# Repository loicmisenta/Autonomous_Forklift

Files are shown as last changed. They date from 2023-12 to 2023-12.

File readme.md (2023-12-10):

---
title: Autonomous forklift
author: Loïc Misenta, Hadrien Saigot Forest, Inés Araujo Cañas, Athena Papageorgiou Koufidou, Kalil Sama Bouzigues, Dylan Vairoli
---

# Introduction
This project was developed for the CS-356 Making Intelligent Things course at EPFL. The team members are Loïc Misenta, Hadrien Saigot Forest, Inés Araujo Cañas, Athena Papageorgiou Koufidou, Kalil Sama Bouzigues and Dylan Vairoli.

# Overview
The autonomous forklift is a project aimed at automating the movement of packets within a facility. When placing a packet in front of the forklift, it uses a camera to read and process a QR code on the packet. The QR code contains information about the packet's intended location in the facility. The forklift then picks it up and moves in a to the designated location and places the packet on the ground. Upon completion, the forklift returns to its starting position, ready to repeat the process with another packet. Manual controls are also available with a gamepad or a web application.

<!-- add video -->
<video src="report/images/AutonomousForkLiftMIT.mp4" controls="controls" style="max-height: 550px;">
</video>

# Materials

### Microcontrollers
- [ESP32-CAM-MB, USB-to-serial interface for ESP32-CAM](https://www.berrybase.de/en/esp32-cam-mb-usb-zu-seriell-schnittstelle-fuer-esp32-cam)
- [ESP32-CAM Development Board incl. OV2640 camera module](https://www.dfrobot.com/product-1879.html)
- [ESP8266](https://en.wikipedia.org/wiki/ESP8266)
- [Arduino Uno](https://en.wikipedia.org/wiki/Arduino_Uno)

### Motors
- [5 NEMA17-04 stepper motors](https://www.3dware.ch/NEMA-17-Stepper-motor-1.8-degree,-1.2A-En.htm)
- [5 stepper drivers](https://www.fruugoschweiz.com/5pcs-a4988-stepstick-stepper-motor-driver-module-with-heat-sink-for-3d-printer-reprap-suitable/p-117051283-245844502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)
- [Arduino Uno CNC shield](https://www.bastelgarage.ch/cnc-shield-a4988-arduino-fur-3d-drucker-und-frasmaschinen-grbl)

### Electronics
- PCB board
- [2 end switches]("https://www.spplotter.com.br/micro-switch-fim-de-curso-omron-ss-5gl)
- jumper cables

### Power supply
- Conrad Energy Lipo battery 11.1V 5000mAh
- 5V to 10V battery

### Construction
- [Machifit 15pcs 400mm Optical Axis Guide Bearing Housings Linear Rail Shaft Support Screws Set](https://www.fruugoschweiz.com/15pcsset-400mm-optical-guide-bearing-axis-screws-linear-guide-rail-shaft-support-set/p-163505313-347691854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)
- 3d printer filament
- MDF
- screws

# Tools
For this project, we used a Prusa 3D printer and a laser cutter, both available at [The SPOT](https://www.epfl.ch/education/educational-initiatives/discovery-learning-program-2/prototyping/page-111858-en-html/) at EPFL. The 3D printer was used to print the wheels and structures for cable and electronic components management, while the laser cutter was used to create the base platform, boxes and forks. Other tools needed for this project include a soldering iron, a multimeter, a screwdriver and other basic tools.
The software you are going to need is the Arduino IDE and a text editor of your choice.
<!-- List of required tools would go here, e.g. laser cutter, 3d printer etc., perhaps also a note about were to obtain them or where to find access to them -->

# Safety
It is important to be aware of potential risks associated with the tools and processes involved. The use of tools such as 3D printers, laser cutters, soldering irons, and other equipment can pose certain hazards. When operating these tools, there is a risk of burns, electric shocks, or injuries from moving parts. To mitigate these risks, it is crucial to follow safety guidelines provided by the tool manufacturers and wear appropriate personal protective equipment (PPE) such as safety glasses, gloves, and closed-toe shoes. Ensure that the work area is well-ventilated and free from clutter, providing a safe environment for operating tools. Take precautions when handling hot or sharp objects, and avoid touching heated surfaces directly. Additionally, exercise caution when working with electrical components or circuits, ensuring proper insulation, grounding, and adherence to safe soldering practices. Regularly inspect and maintain the tools and equipment to ensure they are in good working condition. 

# Construction

<figure>
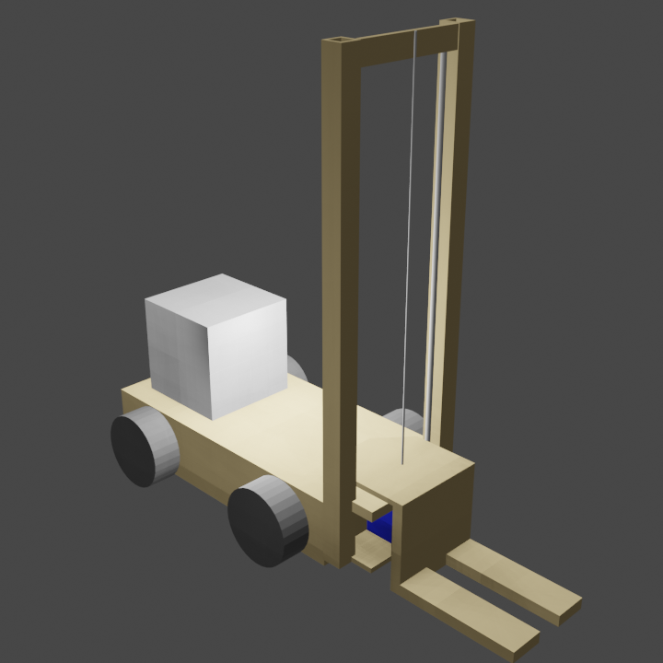
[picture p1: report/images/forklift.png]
  
  <figcaption>Initial idea of the forlift, made with Blender</figcaption>
</figure>

<figure>
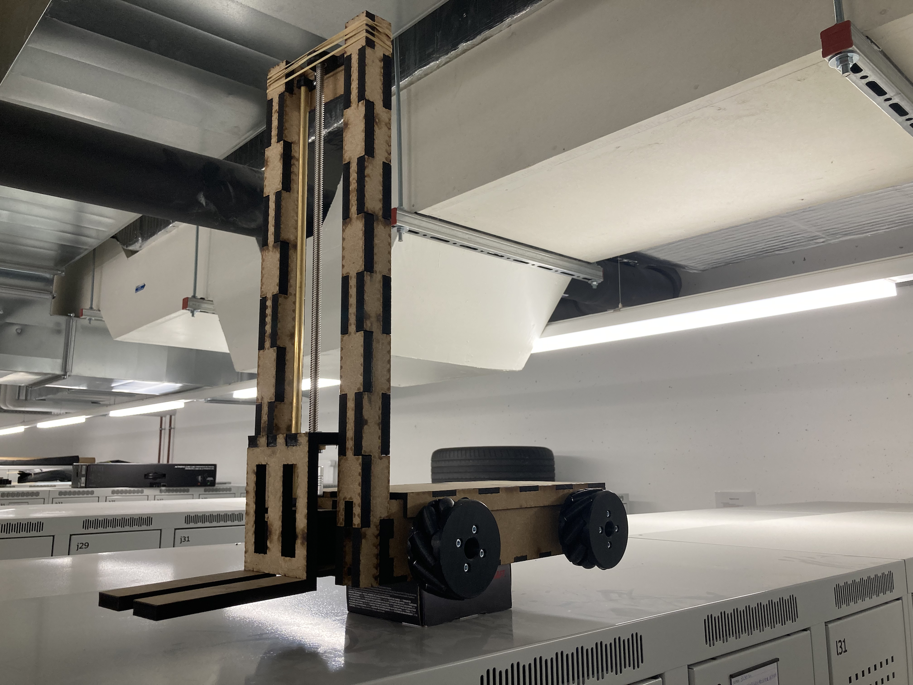
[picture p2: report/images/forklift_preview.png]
  
  <figcaption>Final forklift design.</figcaption>
</figure>

We decided to go with MDF as the primary material for our forklift. It is quite cheap and easily modifiable, while we were prototyping we could quickly drill some new holes and so on.

## Base

<figure>
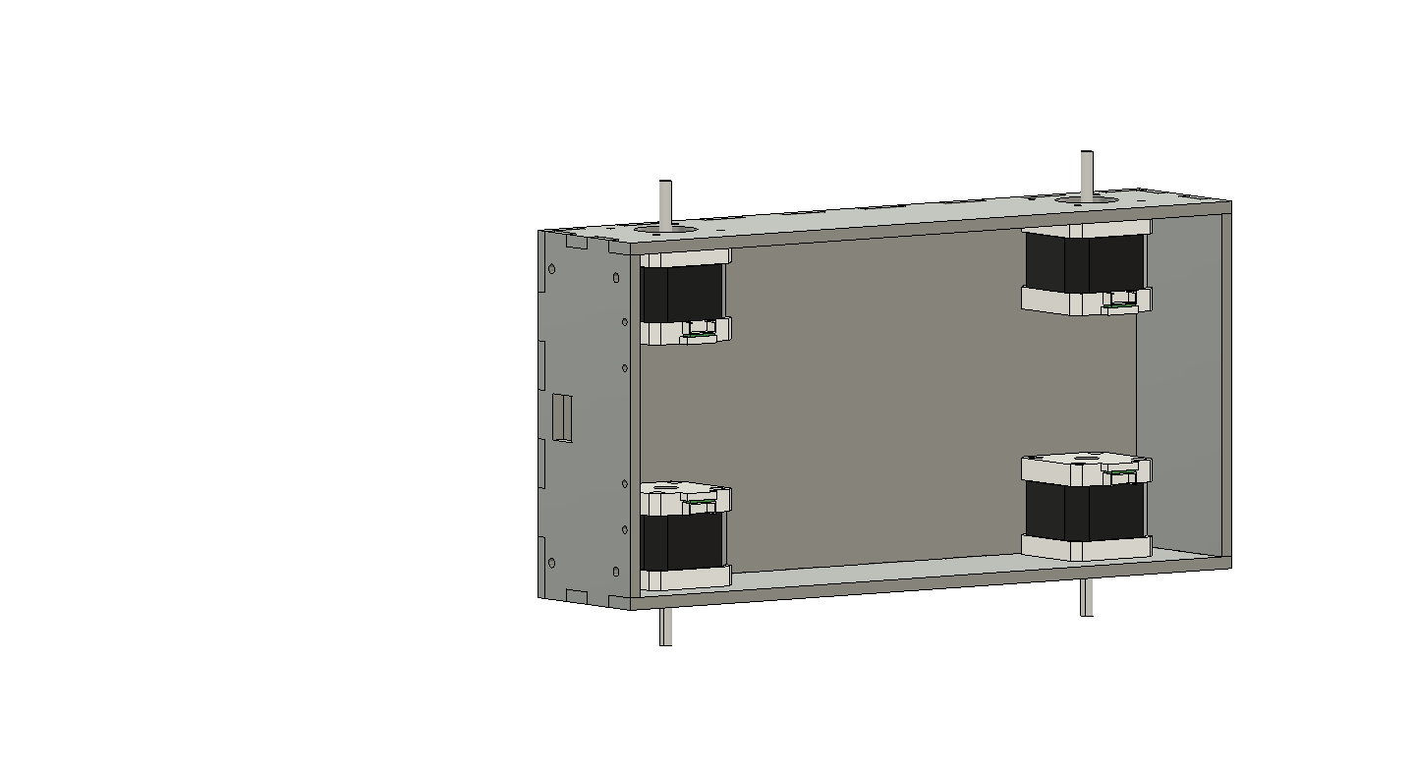
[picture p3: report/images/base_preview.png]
  
  <figcaption>Base of the forklift body.</figcaption>
</figure>

We took the base from the [Arduino Mecanum Wheels Robot](https://howtomechatronics.com/projects/arduino-mecanum-wheels-robot/) project by [Dejan](https://howtomechatronics.com/author/howtom12_wp/) that we slightly adapted to use comb joints and have some more holes so that we can glue parts together and pass cables through it.

You can find the `.dxf` file for this at [`Modeling/Body/base.dxf`](https://gitlab.epfl.ch/papageor/cs-356-autonomous-forklift/-/blob/main/Modeling/Body/base.dxf)

## Side supports

<figure>
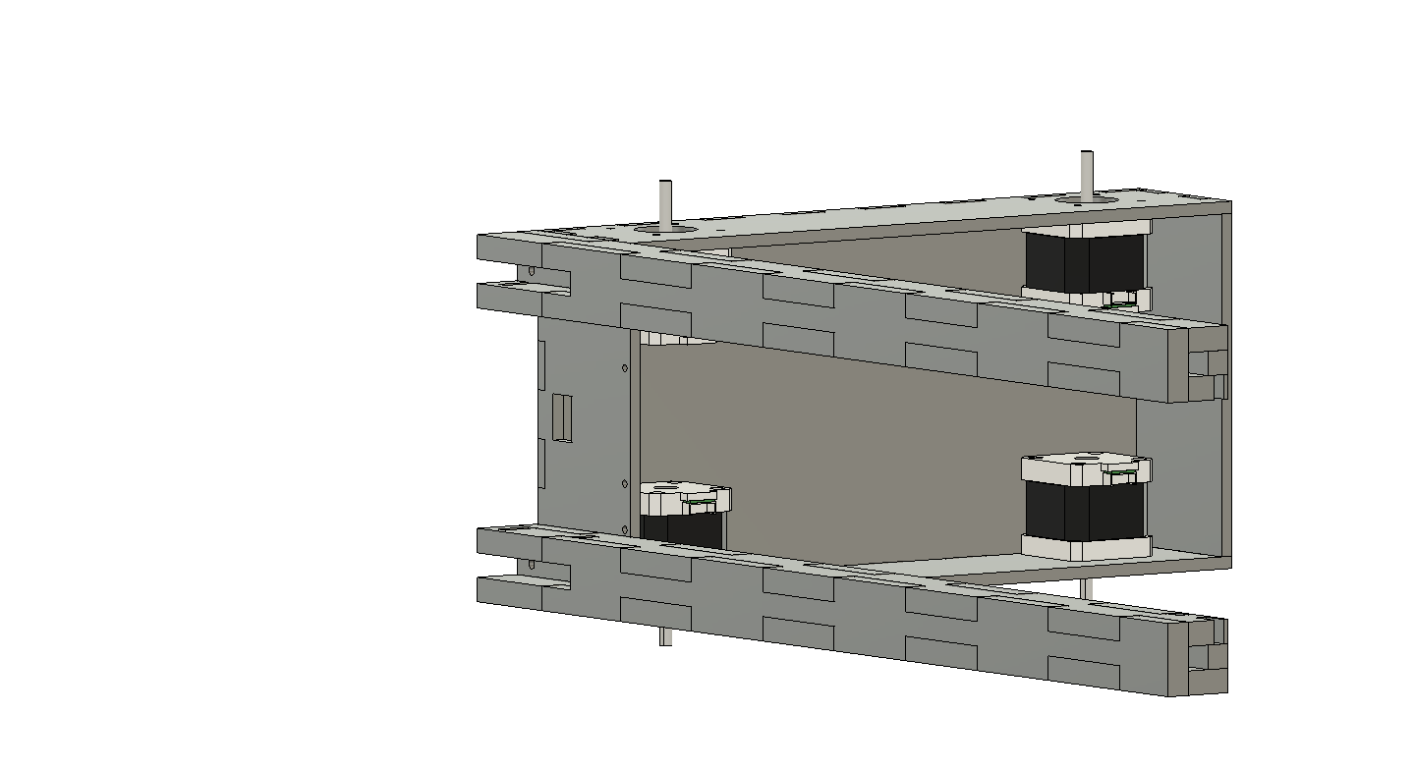
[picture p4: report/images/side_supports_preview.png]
  
  <figcaption>Side supports of the forklift.</figcaption>
</figure>

We designed some side supports to attach the two side shafts on which the forks are drilled. They are quite massive but it was giving a nice raw look to the forklift.

You can find the `.dxf` file for this at [`Modeling/Body/side_supports.dxf`](https://gitlab.epfl.ch/papageor/cs-356-autonomous-forklift/-/blob/main/Modeling/Body/side_supports.dxf)

## Cap

<figure>
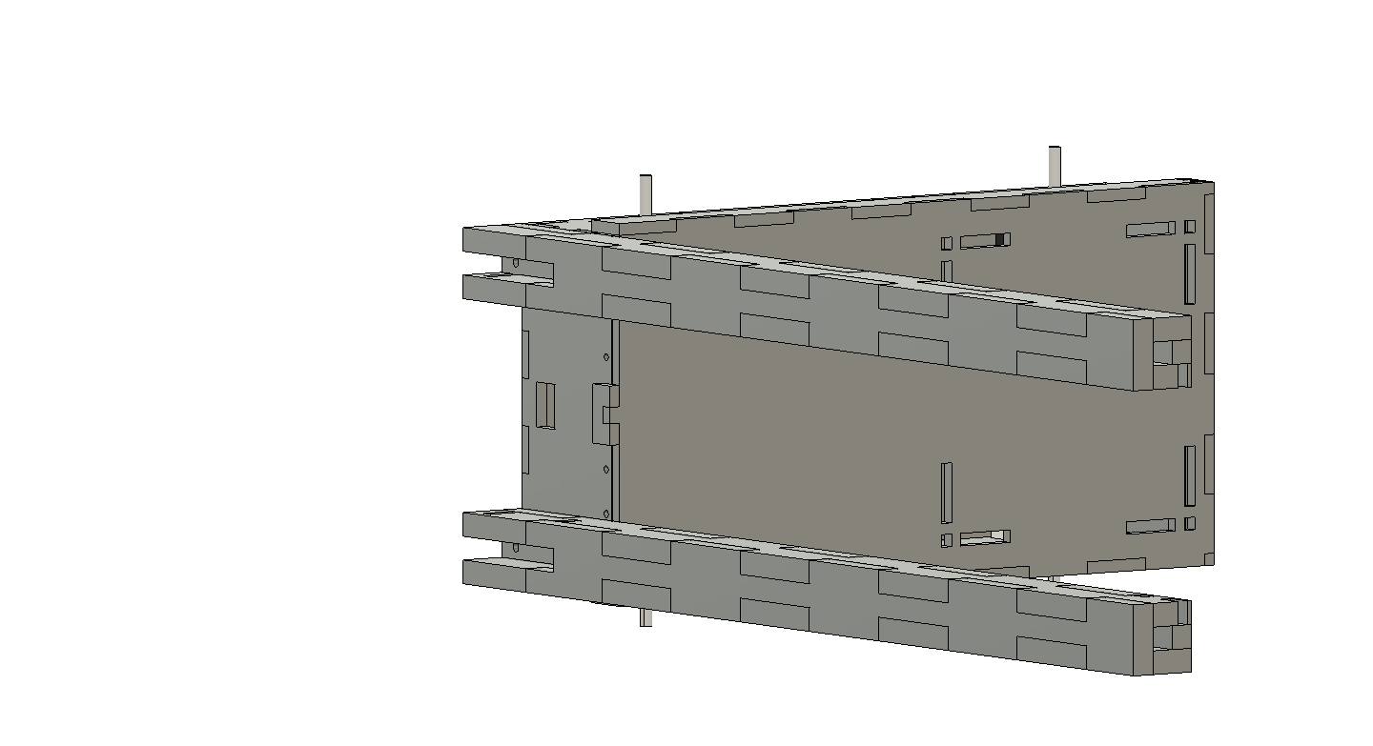
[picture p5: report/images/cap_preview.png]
  
  <figcaption>Cap of the forklift.</figcaption>
</figure>

Also using this comb joints technique, we added a cap that can easily be removed on top of the base platform. It gives a polished and refined aspect to our vehicle by hiding all the cables.

You can find the `.dxf` file for this at [`Modeling/Body/cap.dxf`](https://gitlab.epfl.ch/papageor/cs-356-autonomous-forklift/-/blob/main/Modeling/Body/cap.dxf).

## Forks

<figure>
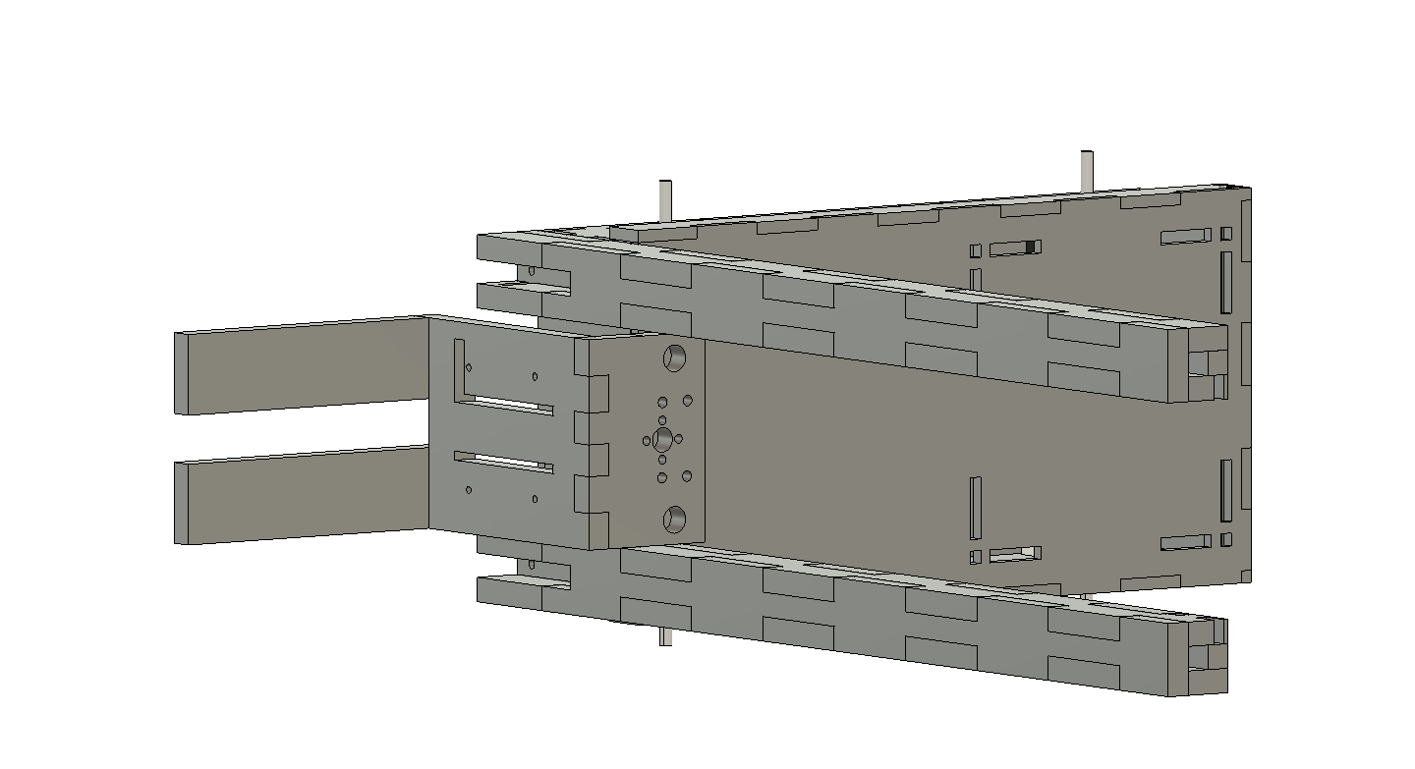
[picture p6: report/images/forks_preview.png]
  
  <figcaption>Forks of the forklift.</figcaption>
</figure>

Obviously, we also had to create the forks that are used to take the boxes. Our first try was a failure because it was too thin and couldn't lift anything without breaking. This final model works better but it still needs brackets to support at least two kilograms. We 3D-printed them because we couldn't get any metal one, but 10x10mm metal brackets are enough.

You can find the `.dxf` file for this at [`Modeling/Body/forks.dxf`](https://gitlab.epfl.ch/papageor/cs-356-autonomous-forklift/-/blob/main/Modeling/Body/forks.dxf). You can also find the `.stl`file for the brackets at [`Modeling/Body/bracket.stl`](https://gitlab.epfl.ch/papageor/cs-356-autonomous-forklift/-/blob/main/Modeling/Body/Bracket.stl).

## Fixation panels

<figure>
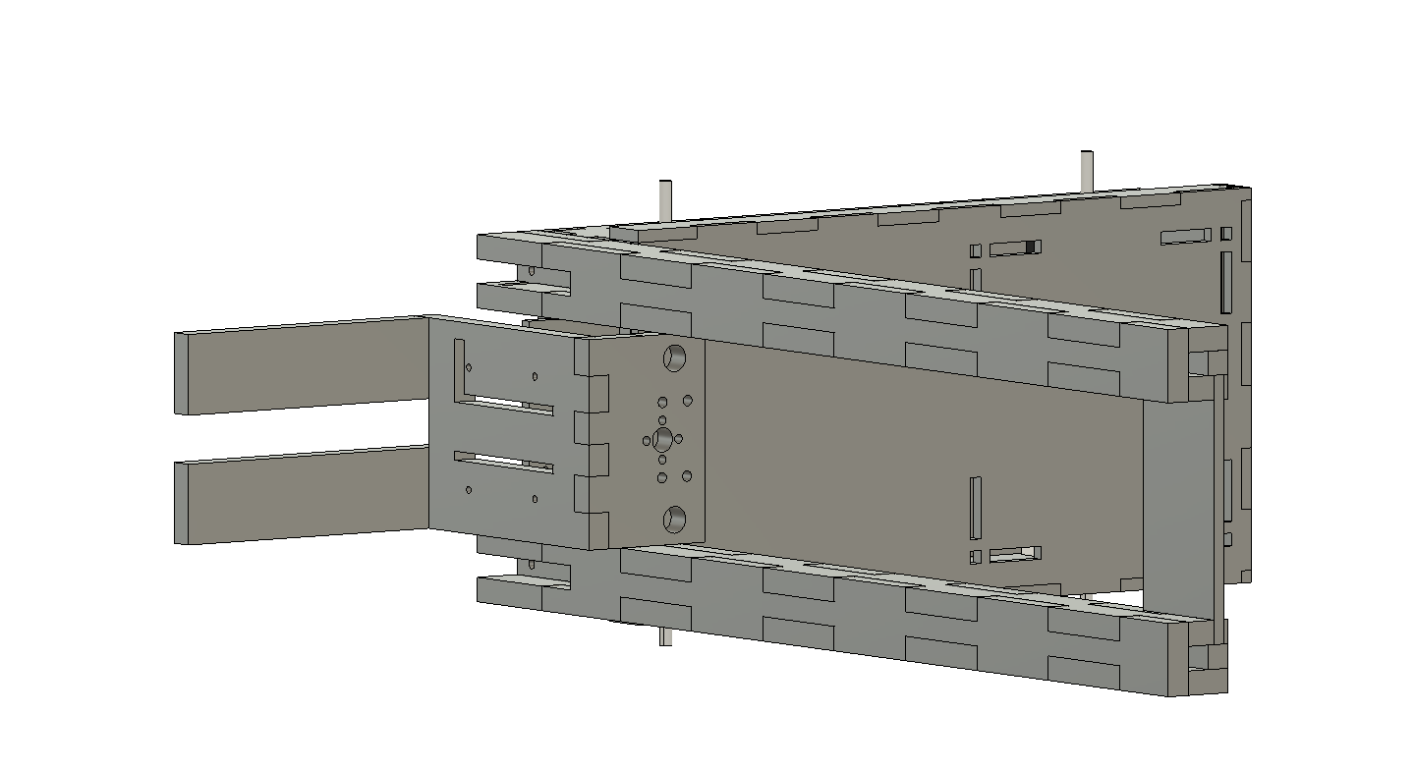
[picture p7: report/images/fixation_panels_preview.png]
  
  <figcaption>Fixation panels of the forklift.</figcaption>
</figure>

Finally, we added some MDF fixation panels to attach our components such as the vertical stepper motor and the three shafts.

You can find the `.dxf` file for this at [`Modeling/Body/fixation_panels.dxf`](https://gitlab.epfl.ch/papageor/cs-356-autonomous-forklift/-/blob/main/Modeling/Body/fixation_panels.dxf).

## Fixations

<figure>
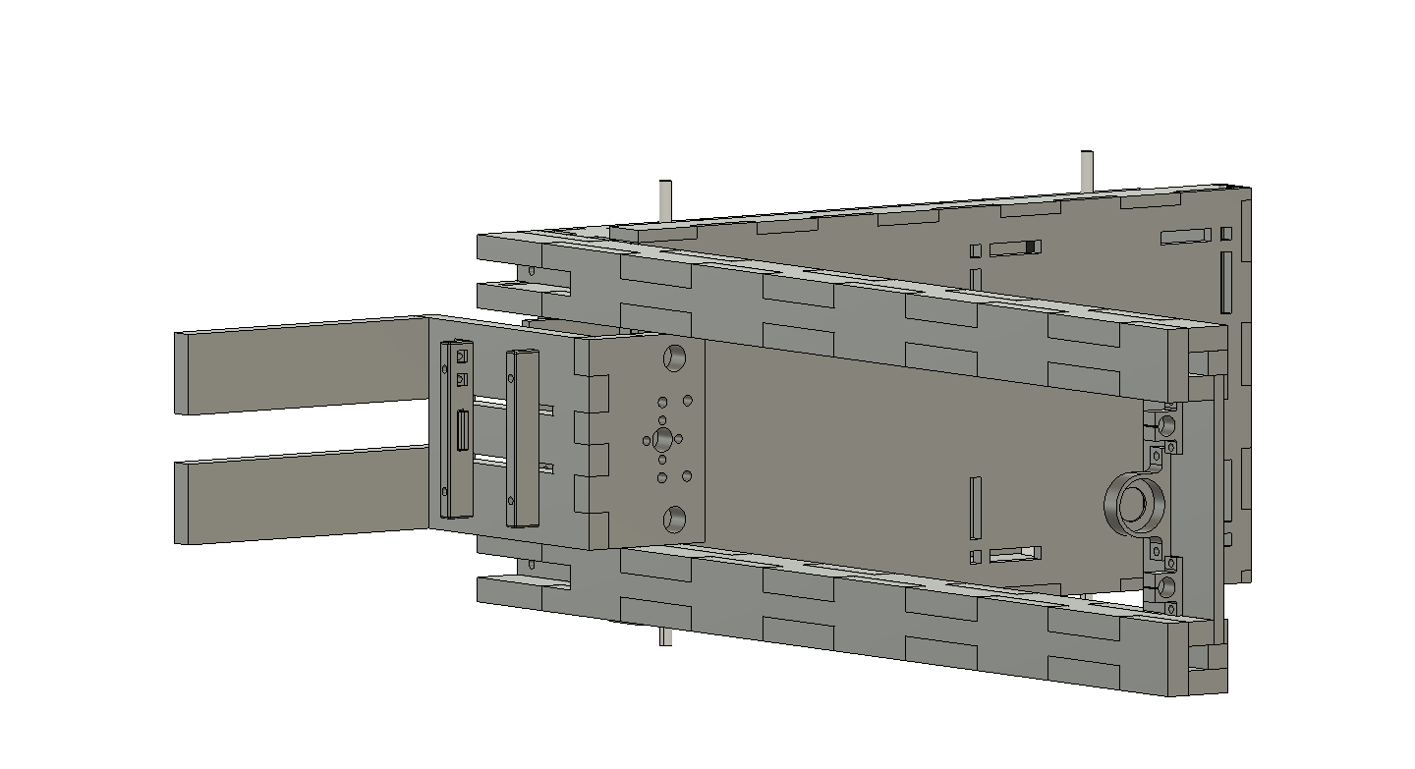
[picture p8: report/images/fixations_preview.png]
  
  <figcaption>Fixations of the forklift.</figcaption>
</figure>

Along the way, we encountered small issues for which we had to design some small 3D-printed pieces
- To hold the two side shafts
- To hold the central screw shaft
- To attach the forks to the block bearings
- To keep the vertical end switch at the right position
- To avoid that the side shafts get out of the fixations when lifting up. Because our block bearings didn't slide perfectly smoothly along our shafts, we needed some caps to force them to stay inside the fixations
- To hold the ESP32-CAM against the forks as well as the horizontal end switch
  
You can find the `.stl` files for these pieces at [`Modeling/Fixations/`](https://gitlab.epfl.ch/papageor/cs-356-autonomous-forklift/-/tree/main/Modeling/Fixations).

## Cable management
To keep our circuit clean and avoid short circuits because of floating components, we designed structures to cleanly manage our cables. 

- One that is used to wrap the cables around
- One to screw our PCB board to the base
- One to attach the ESP8266 to the base

However all of these pieces are very specific to our usecase so it may not suit perfectly your components.
  
You can find the `.stl` files for these pieces at [`Modeling/Cable Management/`](https://gitlab.epfl.ch/papageor/cs-356-autonomous-forklift/-/tree/main/Modeling/Cable%20Management).

## Counterweight box

<figure>
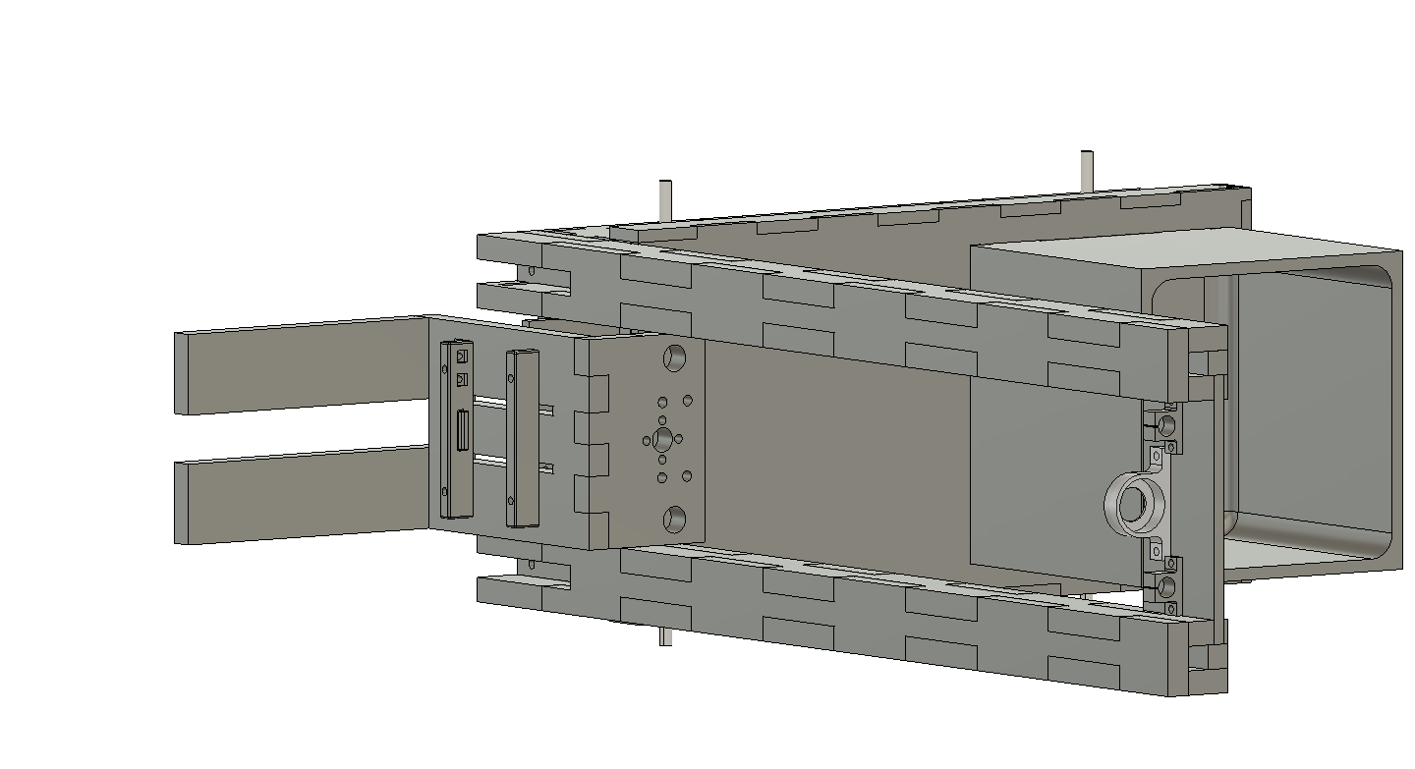
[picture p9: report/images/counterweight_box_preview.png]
  
  <figcaption>Counterweight box of the forklift.</figcaption>
</figure>

Any forklift needs some counterweight at the back of it to balance with the weight it is carrying. To do so, we opted for a 3D-printed box with round edges so that nothing gets stuck in them. You can then fill it with whatever you want, rocks or sand for example.

You can find the `.stl` files for this at [`Modeling/Body/counterweight_box.stl`](https://gitlab.epfl.ch/papageor/cs-356-autonomous-forklift/-/blob/main/Modeling/Body/counterweight_box.stl).

## Mecanum wheels

<figure>
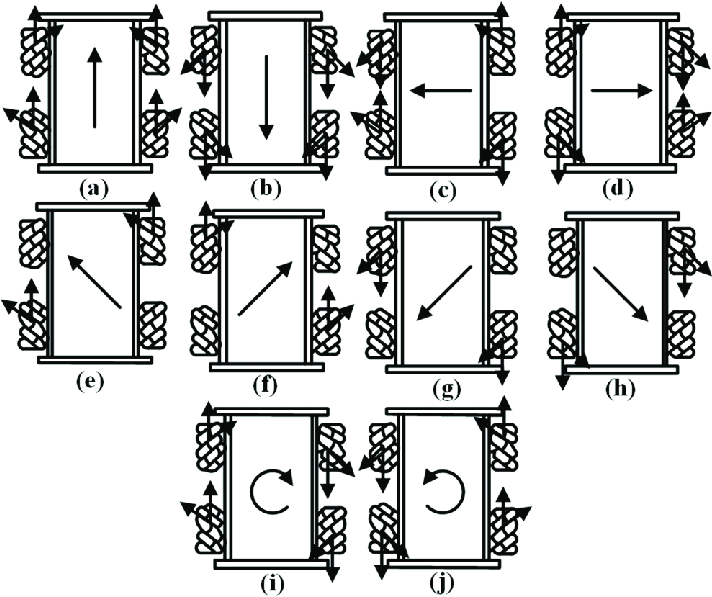
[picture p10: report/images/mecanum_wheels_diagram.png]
  
  <figcaption>Mecanum wheels  combinations diagram (<a href="https://www.researchgate.net/figure/Fig-5-Top-view-of-turning-principle-of-Mecanum-wheel_fig2_307868549">source</a>).</figcaption>
</figure>

Mecanum wheels allow you to move sideways, turn in place as well as go diagonally with only 4 independent wheels. By turning the wheels with a specific combination of directions, you can achieve the desired effect.

We used the [Arduino Mecanum Wheels Robot](https://howtomechatronics.com/projects/arduino-mecanum-wheels-robot/) project as a basis for our wheels. You can either download the `.stl` files from his tutorial or you can find them under [Modeling/Wheels](https://gitlab.epfl.ch/papageor/cs-356-autonomous-forklift/-/tree/main/Modeling/Wheels). Pay attention to print two right wheels and two left wheels. For more details about the mounting of these wheels, you can check [Dejan's tutorial](https://howtomechatronics.com/projects/arduino-mecanum-wheels-robot/).

> Note that we had to slightly modify the outer part of the wheels because we did not have any M3 bolts that were 45mm long, only 40mm.

# Motors and electronics

## A4988 stepper driver
We used A4988 stepper drivers to control our steppers. However we need to limit the output current they produce to 1.5A. To do so we need to adjust the small screw on top of them. Follow the _A4988 Current Limiting_ section of [Stepper Motors and Arduino – The Ultimate Guide by Dejan](https://howtomechatronics.com/tutorials/arduino/stepper-motors-and-arduino-the-ultimate-guide/).

## CNC Shield and Arduino UNO

<figure>
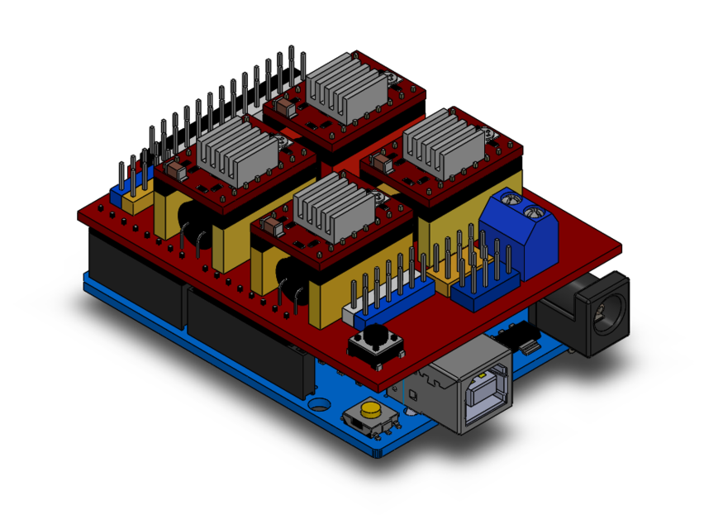
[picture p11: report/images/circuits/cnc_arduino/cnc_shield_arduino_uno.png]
  
  <figcaption>CNC shield and drivers on top of an arduino UNO (<a href="https://grabcad.com/library/arduino-uno-cnc-shield-1">source</a>).</figcaption>
</figure>

<figure>
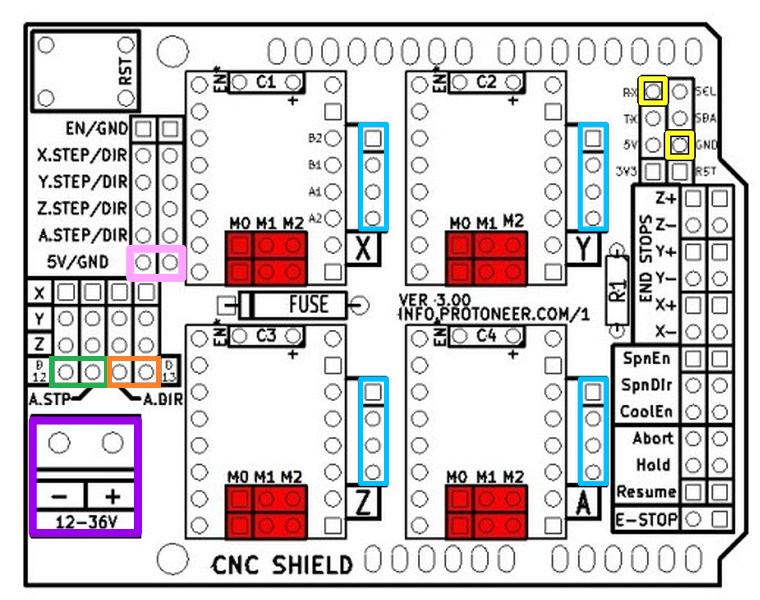
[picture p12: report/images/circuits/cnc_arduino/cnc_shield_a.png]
  
  <figcaption>CNC shield closeup (<a href="https://forum.arduino.cc/t/arduino-uno-cnc-shield-controlling-4-stepper-motors/913742/3">source</a>).</figcaption>
</figure>

The CNC shield is very simple to use, you just need to plug it on top of the Arduino UNO and install the drivers on top of it.

However be careful with a few points:

- The `Enable` pin of the drivers should be at the position marked as `EN` on the shield.
- As we use the 4 steppers independently, we need to indicate that the `A` (red) driver is controlled on its own. This is done by connecting a jumper at the green and orange spots in the image above. ([source](https://www.zyltech.com/arduino-cnc-shield-instructions/)).
- For smoother movement, we decided to use 16x microstepping. This is not mandatory but it works best with the mecanum wheels in our opinion. To do so, you need to connect jumper wires on all the `M0`, `M1` and `M2` pins. You can find more information about other microstepping resolutions [here](https://www.zyltech.com/arduino-cnc-shield-instructions/).
- When plugging in the motors, they might turn in the incorrect direction or you might have plugged steppers in different locations as us. You can test this by uploading the `steppers_test.ino` sketch to the Arduino UNO. It should start turning the steppers clockwise in this order: back left, front left, back right, front right. If they turn counter-clockwise instead, you need to turn their cables by 180 degrees. If they turn in an incorrect order, try to switch the positions where they're plugged in the shield accordingly. 
- You can find the mapping between the Arduino UNO pins number and the actual controls of the shield in the `arduino_main.ino` sketch.

## ESP8266
Unfortunately the Arduino UNO we used does not have WIFI capabilities. As we needed to transfer instructions from the computer using WIFI to our boards, we used an ESP8266. We can consider it as the brain of our circuit, it receives the instructions from the computer online and dispatch it either to the Arduino UNO to move the wheels or to itself to control the vertical stepper. As we just mentioned, it is also responsible to control the vertical stepper motor because the Arduino UNO had all of its pins busy with the shield.

## ESP32-CAM
To scan QR codes we needed a camera, the ESP32-cam was perfect for that as it also has WIFI capabilities. When reading a QR code, it sends its payload (which is simply a number) to the computer which then send the correct instruction to the ESP8266 based on the number it received.

## NEMA 17 stepper motors
We use 5 NEMA17 stepper motors; 4 for the wheels and one for the forks. They are strong motors capable of lifting up our boxes. You can find more information about how stepper motors work [here](https://howtomechatronics.com/how-it-works/electrical-engineering/stepper-motor/)

## Conrad Energy Lipo battery 11.1V 5000mAh
As a power supply for our steppers and the Arduino UNO, we used a 12V Lipo battery.

## 5V to 10V battery
You will also need any kind of 5V to 10V power source for the ESP8266 because it can't take the 12V of the Lipo battery.

## End switches

<figure>
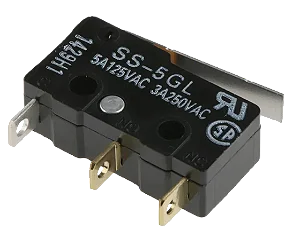
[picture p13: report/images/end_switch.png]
  
  <figcaption>Microswitch Omron SS 5GL (<a href="https://www.spplotter.com.br/micro-switch-fim-de-curso-omron-ss-5gl">source</a>).</figcaption>
</figure>

We used two end switches in our project. The first one is used to know when the forks are at the bottom and we should stop, the other one is used to know when a box is entirely placed on the forks.

# Circuits

## CNC shield
- Connect the stepper cables to the blue area in the above schema.
- Add jumpers between the two green pins and between the two orange pins to control the A slot as well.
- Add jumpers between the `M0`, `M1` and `M2` (red) pins to enable 16x microstepping.
- Connect a 12V power source to the purple area above and to the Arduino UNO.

## ESP8266
- Connect a 5V to 10V power source to the `VIN` and `GND` pins of the ESP8266.

## ESP32
- Connect the `5V` and the `GND` pins of the ESP32 to the `5V` and `GND` pins (pink) of the CNC shield. 

## ESP8266 – Arduino UNO serial communication
- Connect the `D4` and the `GND` pins of the ESP8266 to the `RX` and `GND` pins (yellow) of the CNC shield.

## End switches
- Connect one of the extremity pins of the two end switches to the `3V` pin of the ESP8266.
- Connect the middle pin of the vertical end switch to the `D5` pin of the ESP8266.
- Connect the middle pin of the horizontal end switch to the `D1` pin of the ESP8266.
- Connect the `GND` pin of the ESP8266 to the middle pins of the end switches through a 10k$\Omega$ resistor.

# Software

<figure>
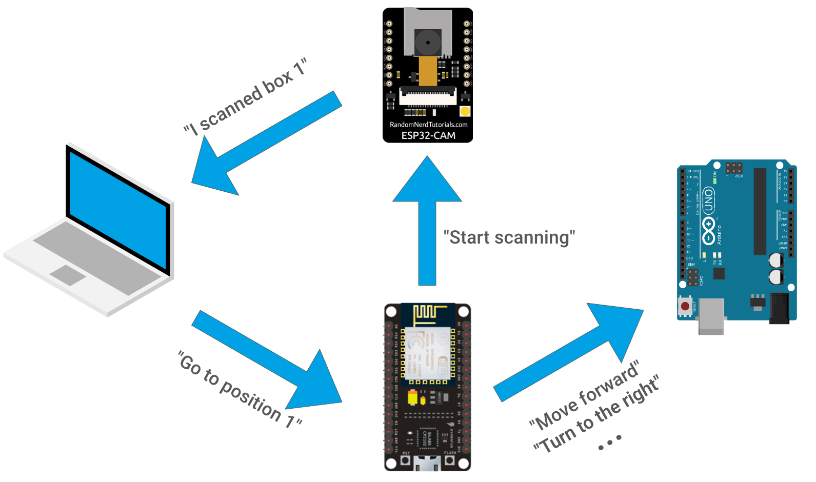
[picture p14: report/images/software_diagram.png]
  
  <figcaption>Software diagram.</figcaption>
</figure>

## Arduino UNO
The Arduino UNO is only responsible to move the wheels of the forklift. It receives instructions from the ESP8266 about where to go using serial communication. We used the `AccelStepper` library to control our steppers.

You can find Arduino-related code at [Code/arduino-main](https://gitlab.epfl.ch/papageor/cs-356-autonomous-forklift/-/tree/main/Code/arduino-main).

## ESP8266
The ESP8266 is the brain of our forklift. It receives instruction from the computer using WIFI and dispatch them correctly to the Arduino UNO if needed, to itself otherwise. It keeps track of the positions of our grid and the current state of the forklift. It also controls the vertical stepper motor.

You can find ESP8266-related code at [Code/esp8266-main](https://gitlab.epfl.ch/papageor/cs-356-autonomous-forklift/-/tree/main/Code/esp8266-main).

## Web clients
To send instructions to the ESP8266's server, we need a web client running on the computer. 

### Web application client
The first one can send intructions by clicking on buttons in a custom UI. You can tell the forklift to go in a particular direction or to pickup a box and to put it at a specific position. It can be found at [Code/webapp](https://gitlab.epfl.ch/papageor/cs-356-autonomous-forklift/-/tree/main/Code/web-clients/webapp).

<figure>
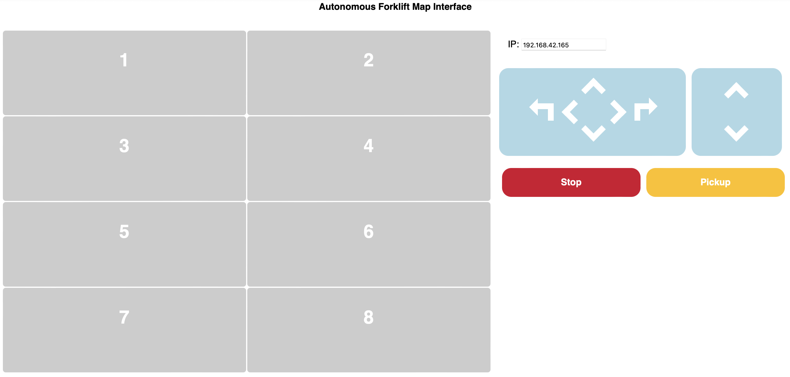
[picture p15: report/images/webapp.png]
  
  <figcaption>Web interface to control the forklift.</figcaption>
</figure>

### Gamepad client
The second one controls the forklift with a gamepad connected to the computer. Simply open [Code/web-clients/gamepad_client.html](https://gitlab.epfl.ch/papageor/cs-356-autonomous-forklift/-/blob/main/Code/web-clients/gamepad_client.html), if a gamepad is detected it will be displayed. Enter the correct IP for your ESP8266 and make sure that it is connected to the same WIFI as your computer. You can change WIFI credentials in [Code/esp8266-main/esp8266-main.ino](https://gitlab.epfl.ch/papageor/cs-356-autonomous-forklift/-/blob/main/Code/esp8266-main/esp8266-main.ino). 

<figure>
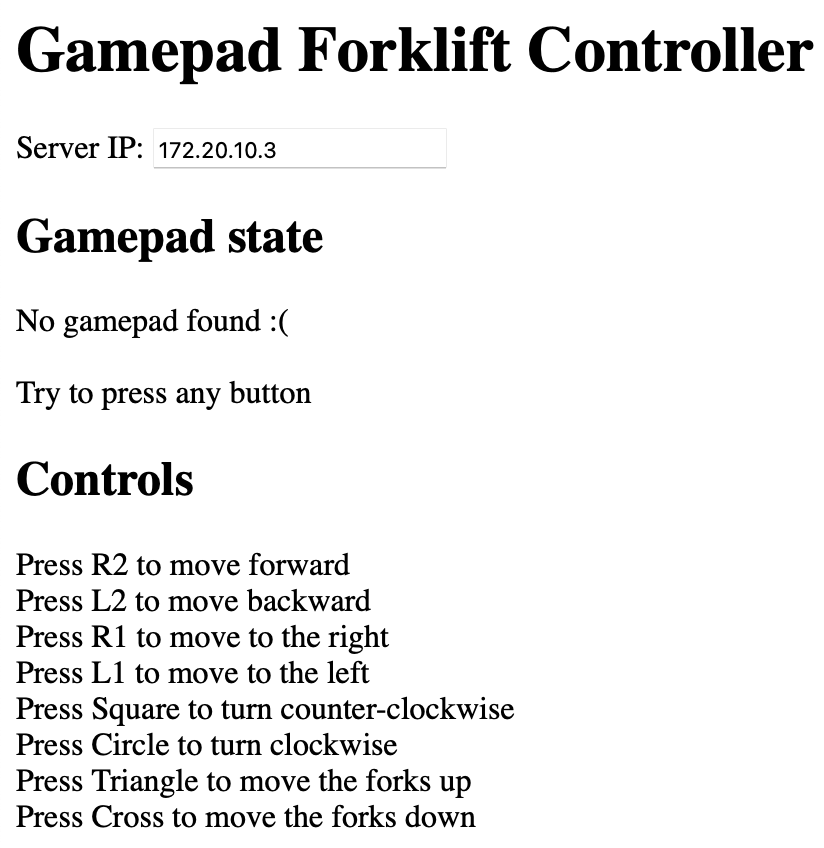
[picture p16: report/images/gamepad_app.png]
  
  <figcaption>Gamepad web controller</figcaption>
</figure>

### QR code recognition
We can also send instructions to the ESP8266 by scanning a QR code. The QR code should contain a number between 1 and 6. The ESP8266 will then move the forklift to the corresponding position in the facility. You can find the code for this at [QR_Code](https://gitlab.epfl.ch/papageor/cs-356-autonomous-forklift/-/tree/main/QR_Code).

The QR code handling is a big part of the project. The way it works is the following. The ESP32-
CAM scan the QR Code present on the box, send the id number of the box to the computer 
which has a .csv file with all the data that corresponds to the box, then send the placement of 
the box to the ESP8266 that can after move appropriately given the information that was in the 
.csv file. The ESP8266 is also responsible for telling the ESP32-CAM to start scanning QR code.

<figure>
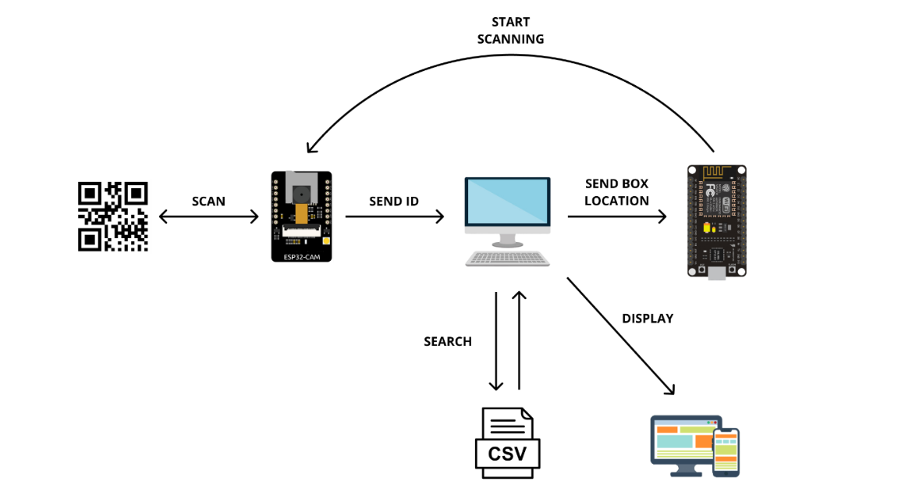
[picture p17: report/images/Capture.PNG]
  
  <figcaption>QR code recognition</figcaption>
</figure>

### Implementation
There is 3 files : [QR_CODE_CSV_2.ino](https://gitlab.epfl.ch/papageor/cs-356-autonomous-forklift/-/blob/main/QR_Code/QR_CODE_CSV_2/QR_CODE_CSV_2.ino), [data.csv](https://gitlab.epfl.ch/papageor/cs-356-autonomous-forklift/-/blob/main/QR_Code/QR_CODE_CSV_2/data.csv), [server.js](https://gitlab.epfl.ch/papageor/cs-356-autonomous-forklift/-/blob/main/QR_Code/QR_CODE_CSV_2/server.js).

#### QR_CODE_CSV_2.ino
In the Arduino file there is multiple sections.  
The first section is the configuration of the server of the ESP32, the connection to the server 
of the computer, the initialisation of camera and the handling of HTTP request coming from the 
ESP8266. 
The second one is the handling of the QR code scan. In this section the scanning will begin 
only if the ESP8266 want a scan. If so it will search for a QR code and if it finds one, it send the 
id found by an HTTP request to the server running on the computer. If there is no error a flash 
will be done to have a visual confirmation that the id was correctly sent. 
The third part is where the server, the client, the camera are all setup correctly to handle all 
situation

#### data.csv
This file contains a table of 3 columns : id, type and description. The id is used to know what 
box it is and where it is going, the type and the description are for the display on the webpage 
to know what is inside. 

#### server.js
This is where the local server on the computer is setup. When it received an http request with 
the id, it will scan each row of the csv file to get all the information needed to send to ESP8266.

### Problems encountered
The main problem that I have encountered is the scanning of the QR Code. I spent a lot of time 
finding and understanding the libraries for scanning. There were many of them so I have to tried 
many to find the best. In this project we wanted to scan quick, also the main question was : 
“What do I put in my QR Code ?”. At first I tried to put a JSON text but the camera detect it very 
slowly so I tried to find some compression algorithms like “shoco” which compress little string 
but not efficient. Finally I found a way to have only a little information on the QR, an id, and all 
the rest on a csv file on the computer. But to do this I have to learn JavaScript and how to create 
a server, with Node in my case.  
Another problem was the voltage of the ESP32-CAM. This one randomly give an infinite loop of 
error misunderstanding. At first I was thinking it was my code, so I spent few days to recode all. 
After a deep search I found that this ESP32-CAM needs 5V and not 3V when it used a lot of 
resources, like QR Code scanning. But I was using my ESP8266 to send, and decode code so 
it was relies with the 3V of the ESP8266. 
I wrote these line for you to know where I spent my time and to help others students in the 
future to not spending weeks and weeks to debug.

## Navigation
There are several navigation options that can be used to guide the vehicle to the correct path. Since the forklift will be moving in a known facility, we decided to use a form of graph-based navigation, i.e. to divide the facility into a grid of possible positions or nodes, with edges connecting the nodes representing possible paths that the forklift can take. The forklift can use this graph to find the shortest path to a destination node based on its current position and the instructions associated with each node. This approach is simple and easy to implement, as it does not require complex sensors or computer vision algorithms and efficient, as the graph can be precomputed and stored, making the navigation process faster. 

This form of navigation proved to be sufficient for our use case, as the forklift was able to reach its destination with accuracy and without any issues. However, it is not the most robust solution, as it does not account for obstacles or other dynamic changes in the environment. For example, if a box is placed in the middle of the path, the forklift will not be able to detect it and will continue to move forward, potentially colliding with the box. To address this issue, we could use a combination of graph-based navigation and computer vision, where the forklift can use the graph to find the shortest path to the destination and use computer vision to detect obstacles and avoid collisions. This approach would be more robust, as it would allow the forklift to adapt to changes in the environment and avoid obstacles. However, it would also be more complex to implement, as it would require more sensors and computer vision algorithms.

Another possible implementation was using a map where each position are represented as 2D vectors, the x-component is the horizontal distance to travel for the forklift to reach the box in that position and the y-component is the vertical distance to travel from the starting point to where the box stands in that given position. This way we can make any large number of boxes and the map will be made accordingly using a function with a for-loop. The thing is that, in real life the wheels slip a little§ bit on the floor, and even if each box are spaced by a certain equal distance, the vertical distance to each box are not exactly multiple of the vertical step. In that way, we had to recalibrate those steps with some arbtrary coefficient and measure every vertical distance to each position. 

# Conclusion
This project was a great opportunity to learn about the different aspects of robotics, from the mechanical design and construction of the forklift to the electronics and software implementation. We were able to apply the concepts learned in class to a real-world application, which allowed us to gain a better understanding of the material. We also learned how to use new tools and technologies, such as Fusion 360, Arduino, and ESP8266, which will be useful for future projects. Overall, we are satisfied with the results of the project, as we were able to successfully implement the forklift and achieve our goal of automating the movement of packets within a facility.

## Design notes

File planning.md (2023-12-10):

# Current status
- The ESP32 can read QR Code information (that is encoded) and send the information (that is decoded) on the webserver
- The platform is able to move in any direction using the mecanum wheels.
- The fork assembly is attached to the base platform.
- Some boxes to test the fork assembly have been created.

# Planning
## Weeks 10 and 11

At the end of week 11, we should have a working prototype of the forklift that can move around the facility and place boxes to the requested location. The forklift will be able to navigate the facility using a grid system and communicate with a server to receive instructions. The forklift will be able to detect the location of the boxes using a camera and QR codes.

### Navigation: (Athena)
- Implement the algorithm for navigating the grid.
- Write code to improve the accuracy of the navigation algorithm by testing and fine-tuning values.

### Communication: (Dylan and Loic)
- Establish communication between ESP32 and Arduino Uno by writing code for both devices to send and receive data and figuring out the electronics needed (Arduino UNO doesn't have wifi).
- Run a server to test the communication between the devices by sending different types of data.
- Develop a plan for adding the camera, including designing the circuit and writing the code to transmit data from ESP32 to ESP8266 to Arduino.

### Boxes and Facility:(Hadrien)
- Redesign the boxes to be compatible with the new forks by analyzing the dimensions and determining what changes are necessary.
- Create a design for the facility in which the forklift will move by considering the size of the space, obstacles, and the location of the boxes. (we need a floor!!!)

### Forks (Ines and Hadrien and Kalil):
- Ensure that the fork assembly can move vertically to the requested height by designing and implementing a motor control system.
- Add end-switches to the forks to recalibrate the motor at the bottom and detect when the forks are at the bottom of a box by designing and implementing a circuit and code to interface with the switches.

### Camera and QR code (Loic)
- Create a database based on ID  and location of the boxes. The QR code will will contain th eID of the box
- Make the webserver able to send the location of the box to the forklift

### Documentation (all)
- Create documentation for all components of the system, including the code, hardware, and design files.
- Ensure that the documentation is clear, concise, and easy to understand.

### Testing (all)
- Conduct comprehensive testing of the entire system, including navigation, communication, and fork operation.
- Identify and fix any issues discovered during testing.

## Weeks 12 and 14

The schedule for the last weeks will depend on the progress made during the first two weeks. If the forklift is not fully functional by the end of week 11, we will continue working on the tasks from the previous weeks. If the forklift is fully functional, we will work on the following extensions:

- The forklift should be able to stack boxes on top of each other.
- The forklift should be able to pick up boxes from the self and bring them back to the starting point.

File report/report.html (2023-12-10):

# Autonomous forklift

Loïc Misenta, Hadrien Saigot Forest, Inés Araujo Cañas, Athena Papageorgiou Koufidou, Kalil Sama Bouzigues, Dylan Vairoli

# Introduction

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

# Overview

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

# Materials

### Microcontrollers

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

### Motors

- 5 NEMA17-04 stepper motors (https://www.3dware.ch/NEMA-17-Stepper-motor-1.8-degree,-1.2A-En.htm)
- 5 stepper drivers (https://www.fruugoschweiz.com/5pcs-a4988-stepstick-stepper-motor-driver-module-with-heat-sink-for-3d-printer-reprap-suitable/p-117051283-245844502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)
- Arduino Uno CNC shield (https://www.bastelgarage.ch/cnc-shield-a4988-arduino-fur-3d-drucker-und-frasmaschinen-grbl)

### Electronics

- PCB board
- 2 end switches
- jumper cables

### Power supply

- Conrad Energy Lipo battery 11.1V 5000mAh
- 5V to 10V battery

### Construction

- Machifit 15pcs 400mm Optical Axis Guide Bearing Housings Linear Rail Shaft Support Screws Set (https://www.fruugoschweiz.com/15pcsset-400mm-optical-guide-bearing-axis-screws-linear-guide-rail-shaft-support-set/p-163505313-347691854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)
- 3d printer filament
- MDF
- screws

# Tools

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

# Safety

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

# Construction

my alt text

Initial idea of the forklift, made with Blender.

my alt text

Final forklift design.

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

## Base

my alt text

Base of the forklift body.

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

## Side supports

my alt text

Side supports of the forklift.

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

## Cap

my alt text

Cap of the forklift.

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

## Forks

my alt text

Forks of the forklift.

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

You can find the .dxf file for this at Modeling/Body/forks.dxf (https://gitlab.epfl.ch/papageor/cs-356-autonomous-forklift/-/blob/main/Modeling/Body/forks.dxf). You can also find the .stlfile for the brackets at Modeling/Body/bracket.stl (https://gitlab.epfl.ch/papageor/cs-356-autonomous-forklift/-/blob/main/Modeling/Body/Bracket.stl).

## Fixation panels

my alt text

Fixation panels of the forklift.

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

## Fixations

my alt text

Fixations of the forklift.

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

## Cable management

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

## Counterweight box

my alt text

Counterweight box of the forklift.

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

## Mecanum wheels

my alt text

Mecanum wheels combinations diagram (source (https://www.researchgate.net/figure/Fig-5-Top-view-of-turning-principle-of-Mecanum-wheel_fig2_307868549)).

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

# Motors and electronics

## A4988 stepper driver

We used A4988 stepper drivers to control our steppers. However we need to limit the output current they produce to 1.5A. To do so we need to adjust the small screw on top of them. Follow the A4988 Current Limiting section of Stepper Motors and Arduino – The Ultimate Guide by Dejan (https://howtomechatronics.com/tutorials/arduino/stepper-motors-and-arduino-the-ultimate-guide/).

## CNC Shield and Arduino UNO

my alt text

CNC shield and drivers on top of an arduino UNO (source (https://grabcad.com/library/arduino-uno-cnc-shield-1)).

my alt text

CNC shield closeup (source (https://forum.arduino.cc/t/arduino-uno-cnc-shield-controlling-4-stepper-motors/913742/3)).

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

However be careful with a few points:

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

## ESP8266

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

## ESP32-CAM

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

## NEMA 17 stepper motors

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

## Conrad Energy Lipo battery 11.1V 5000mAh

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

## 5V to 10V battery

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

## End switches

my alt text

Microswitch Omron SS 5GL (source (https://www.spplotter.com.br/micro-switch-fim-de-curso-omron-ss-5gl)).

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

# Circuits

## CNC shield

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

## ESP8266

- Connect a 5V to 10V power source to the VIN and GND pins of the ESP8266.

## ESP32

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

## ESP8266 – Arduino UNO serial communication

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

## End switches

- Connect one of the extremity pins of the two end switches to the 3V pin of the ESP8266.
- Connect the middle pin of the vertical end switch to the D5 pin of the ESP8266.
- Connect the middle pin of the horizontal end switch to the D1 pin of the ESP8266.
- Connect the GND pin of the ESP8266 to the middle pins of the end switches through a 10kΩ resistor.

# Software

my alt text

Software diagram.

## Arduino UNO

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

## ESP8266

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

## Web clients

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

### Web application client

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

my alt text

Web interface to control the forklift.

### Gamepad client

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

my alt text

Gamepad web controller

### QR code recognition

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

QR code recognition

QR code recognition

### Implementation

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

#### QR_CODE_CSV_2.ino

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

#### data.csv

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

#### server.js

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

### Problems encountered

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

## Navigation

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

# Conclusion

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

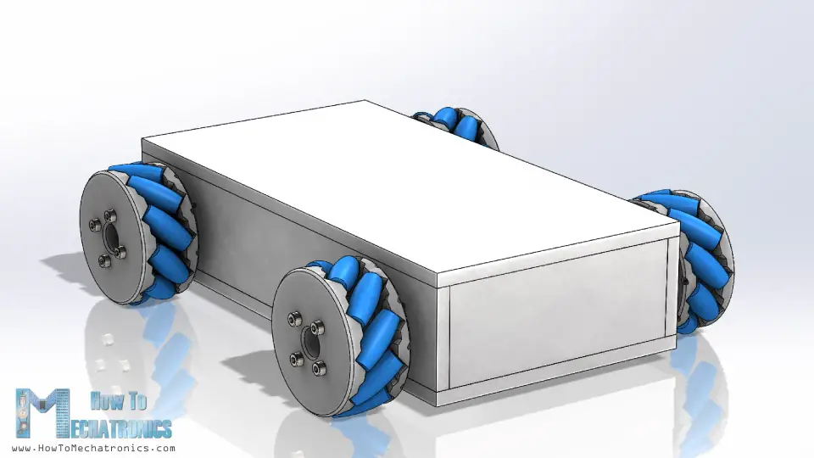
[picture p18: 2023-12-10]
report/images/mecanum_model.png

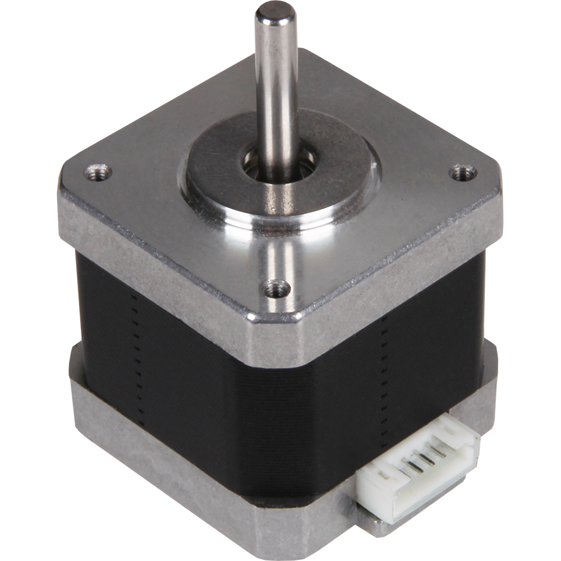
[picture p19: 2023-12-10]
report/images/nema17.png

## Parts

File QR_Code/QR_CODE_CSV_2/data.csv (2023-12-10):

id | type | description
1 | "PAPER" | "Recycled paper from EPFL"
2 | "ROCK" | "Rock from Russia"
3 | "ROCK" | "Rock from Everest"
4 | "SAND" | "Sand imported from Sahara"

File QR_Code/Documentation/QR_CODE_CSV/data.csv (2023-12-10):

id | row | shelf | type | description | action
1 | 1 | 4 | "PAPER" | "Recycled paper from EPFL" | "stay"
2 | 2 | 3 | "ROCK" | "Rock from Russia" | "move"
3 | 3 | 2 | "ROCK" | "Rock from Everest" | "stay"
4 | 2 | 2 | "SAND" | "Sand imported from Sahara" | "move"

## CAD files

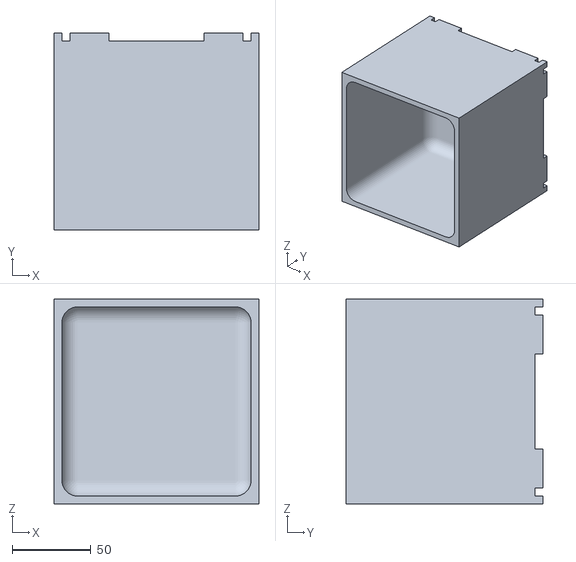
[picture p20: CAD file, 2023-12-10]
Modeling/Body/counterweight_box.stl
130.0 x 125.0 x 130.0

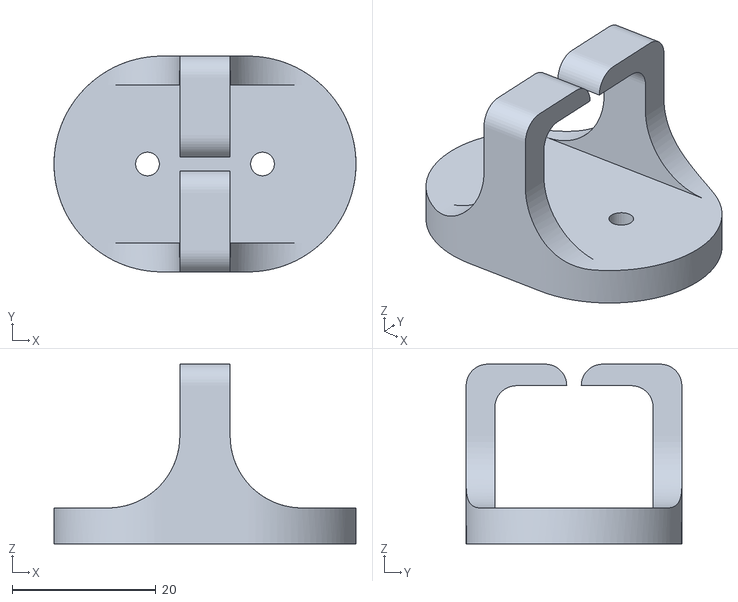
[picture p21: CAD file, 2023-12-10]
Modeling/Cable Management/Wire holder Wider.stl
42.0 x 30.0 x 25.0

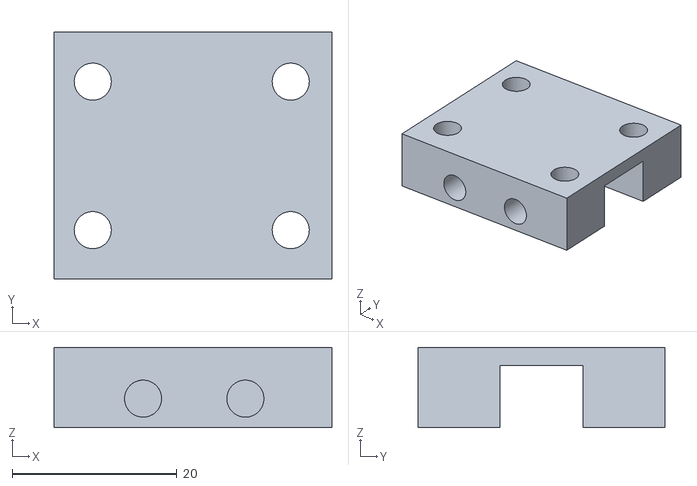
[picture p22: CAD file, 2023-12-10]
Modeling/Fixations/fork_fixation.stl
33.7 x 29.9 x 9.70

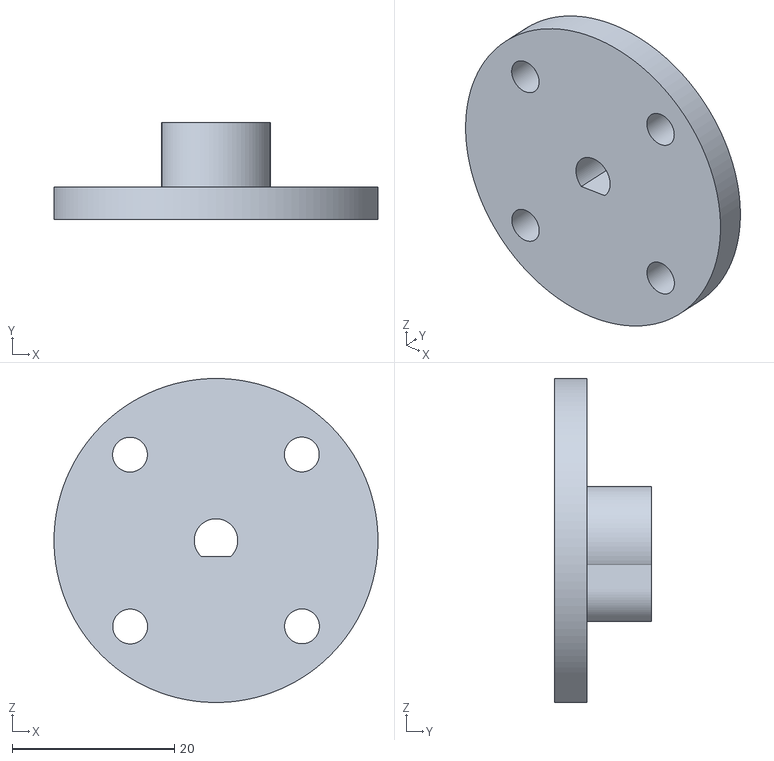
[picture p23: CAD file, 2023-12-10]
Modeling/Wheels/Shaft Coupler Nema 17.STL
40.0 x 12.0 x 40.0

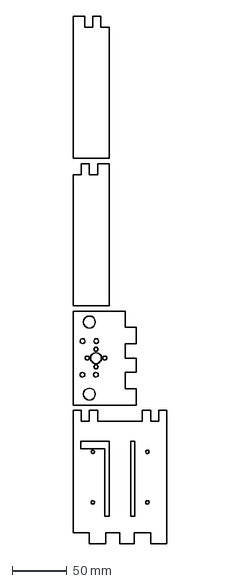
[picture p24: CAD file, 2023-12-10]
Modeling/Body/forks.dxf
86.0 x 483.0 mm

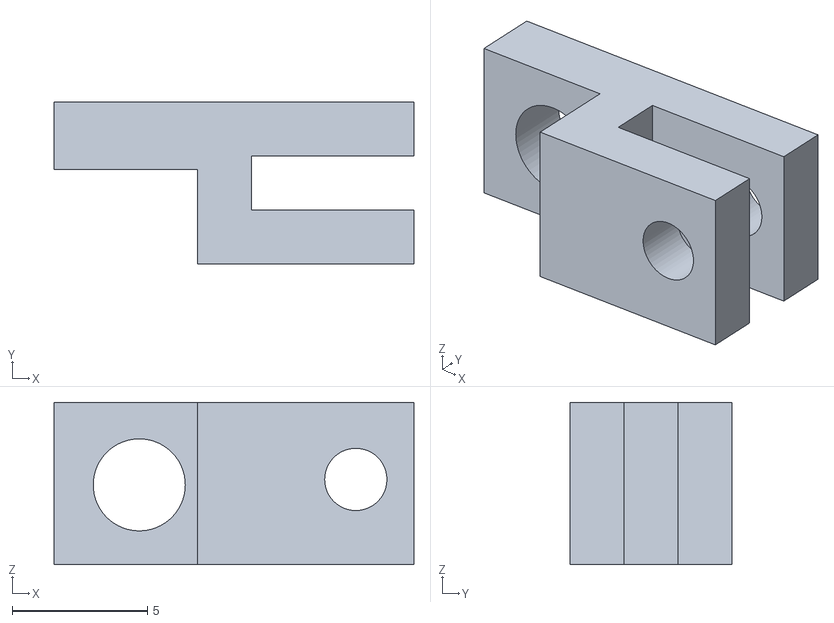
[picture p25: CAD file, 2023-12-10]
Modeling/Cable Management/PCB support.stl
13.3 x 6.00 x 6.00

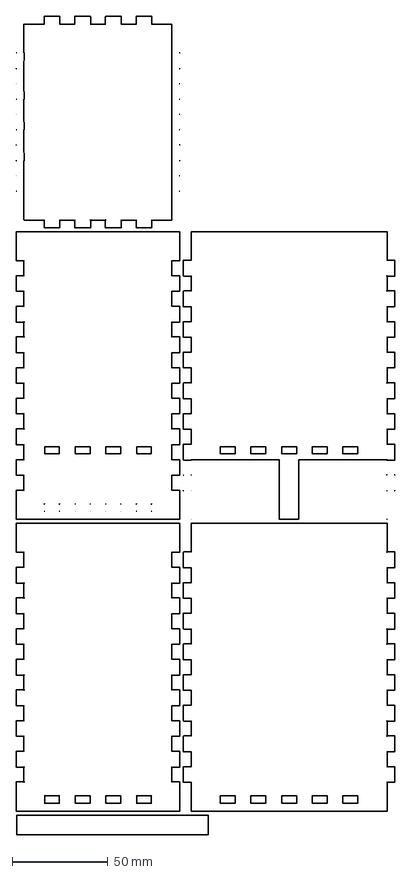
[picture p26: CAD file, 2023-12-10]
Modeling/Environment/box.dxf
197.4 x 426.8 mm

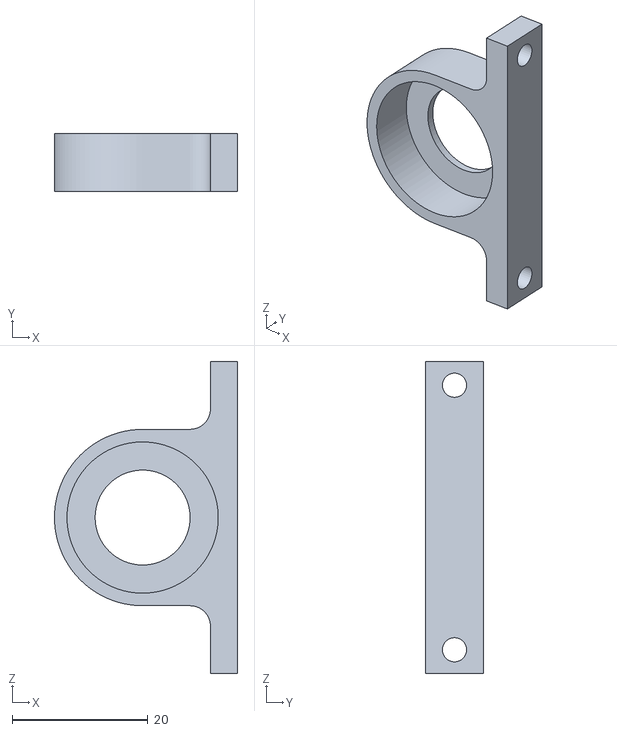
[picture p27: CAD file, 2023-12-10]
Modeling/Fixations/center_shaft_fixation.stl
27.0 x 8.50 x 46.0

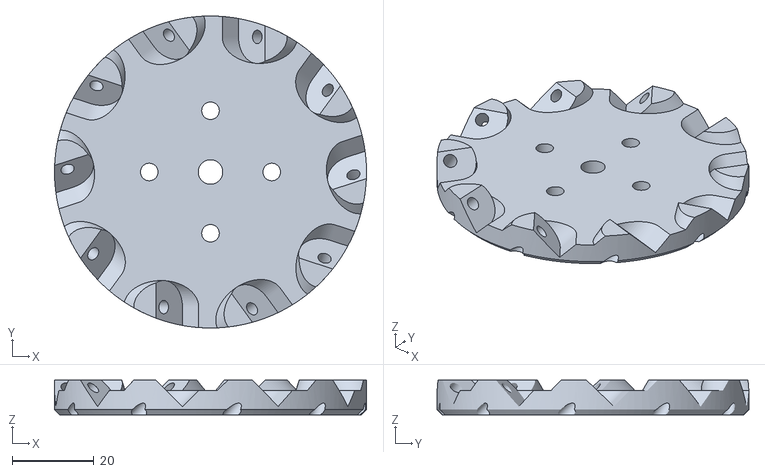
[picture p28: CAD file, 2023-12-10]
Modeling/Wheels/Wheel base plate Right.STL
76.4 x 76.4 x 8.50

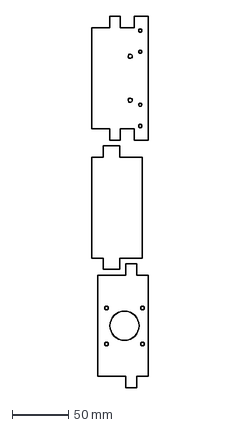
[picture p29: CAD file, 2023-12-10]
Modeling/Body/fixation_panels.dxf
50.0 x 330.0 mm

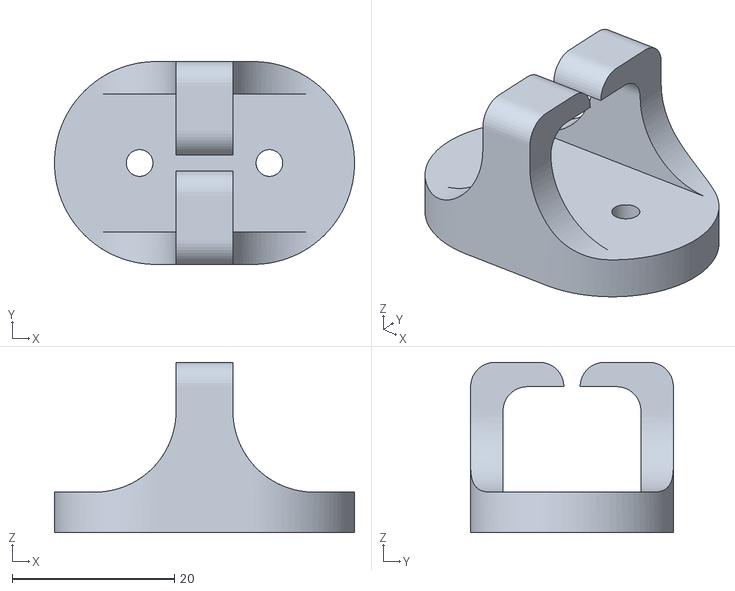
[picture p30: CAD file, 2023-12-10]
Modeling/Cable Management/Wire holder.stl
37.0 x 25.0 x 21.0

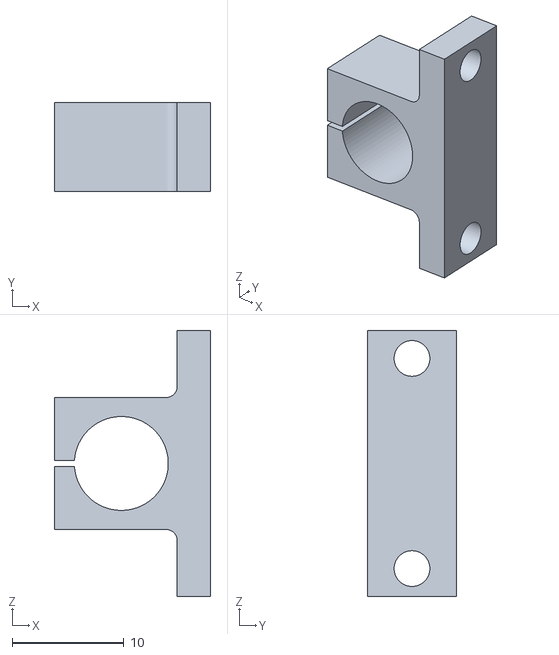
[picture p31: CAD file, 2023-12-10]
Modeling/Fixations/side_shaft_fixation_top.stl
14.0 x 8.00 x 23.8

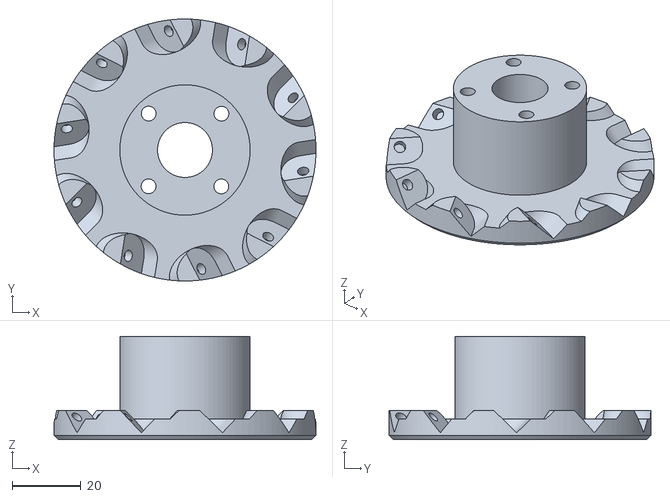
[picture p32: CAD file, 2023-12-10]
Modeling/Wheels/Wheels outer side Right.stl
76.4 x 76.4 x 30.2

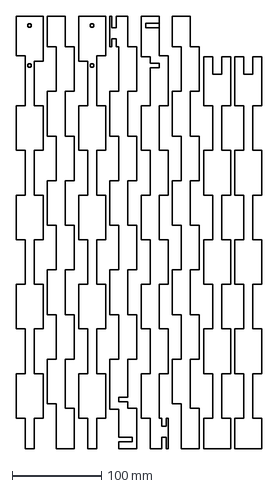
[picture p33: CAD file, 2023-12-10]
Modeling/Body/side_supports.dxf
275.0 x 484.0 mm

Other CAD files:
Modeling/Environment/floor.dxf
Modeling/Cable Management/esp8266 support.stl
Modeling/Fixations/shaft_cap.stl
Modeling/Wheels/Wheel outer side Left.stl
Modeling/Body/Bracket.stl
Modeling/Body/base.dxf
Modeling/Body/cap.dxf
Modeling/Fixations/side_shaft_fixation_bottom.stl
Modeling/Fixations/side_shaft_switch_fixation.stl
Modeling/Wheels/Roller.STL
Modeling/Wheels/Wheel base plate Left.STL

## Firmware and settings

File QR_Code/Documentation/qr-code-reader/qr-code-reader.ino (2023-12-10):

#include <Arduino.h>
#include <ESP32QRCodeReader.h>

#include <DNSServer.h>
#ifdef ESP32
#include <WiFi.h>
#include <AsyncTCP.h>
#elif defined(ESP8266)
#include <ESP8266WiFi.h>
#include <ESPAsyncTCP.h>
#endif
#include "ESPAsyncWebServer.h"

#include <ArduinoJson.h>


StaticJsonDocument<200> doc;

ESP32QRCodeReader reader(CAMERA_MODEL_AI_THINKER);

// Set these to your desired credentials.
const char *ssid = "Lolo";
const char *password = "jesuispauvre";

// Create AsyncWebServer object on port 80
AsyncWebServer server(80);

// Create an Event Source on /events
AsyncEventSource events("/events");

String scan1 = "No Scan";
String scan2 = "No Scan";
String scan3 = "No Scan";
char scan[] = "No Scan";

bool newQR = false;


//annex functions

bool decodeJson(char json[]){
 

  DeserializationError error = deserializeJson(doc, json);

  if (error) {
    Serial.print(F("deserializeJson() failed: "));
    Serial.println(error.f_str());
    return false;
  }
  return true;
}

int getStorageCabinet(){
  return doc["StorageCabinet"];
}

int getFloor(){
  return doc["Floor"];
}
const char* getType(){
  return doc["Type"];
}
const char* getDescription(){
  return doc["Description"];
}


void encodeData(int storageCabinet, int floor, const char* type, char* BUFFER){
  sprintf(BUFFER, "%d %d %s", storageCabinet, floor, type);
}

void decodeData(int* storageCabinetAndFloor, char* type, char* BUFFER){
    char typeBuffer[32];
    int storageCabinet;
    int floor;
    sscanf(BUFFER, "%d %d %s", &storageCabinet, &floor, typeBuffer);
    storageCabinetAndFloor[0] = storageCabinet;
    storageCabinetAndFloor[1] = floor;
    strcpy(type, typeBuffer);
}


// Initialize WiFi (STATIC IP) -- not used, don't work...
void initWiFi() {

    WiFi.softAP("Lolo", password);

    delay(2000);
    // Set static IP
    IPAddress AP_LOCAL_IP(192, 168, 1, 1);
    IPAddress AP_GATEWAY_IP(192, 168, 1, 4);
    IPAddress AP_NETWORK_MASK(255, 255, 255, 0);
    if (!WiFi.softAPConfig(AP_LOCAL_IP, AP_GATEWAY_IP, AP_NETWORK_MASK)) {
        Serial.println("AP Config Failed");
        return;
    }
    Serial.println("WiFi AP setup");
    IPAddress IP = WiFi.softAPIP();
    Serial.print("AP IP address: ");
    Serial.println(IP);

    while (WiFi.status() != WL_CONNECTED) {
        Serial.print('.');
        delay(1000);
    }
    Serial.println(WiFi.localIP());
    
}


void initWiFi2(){
  WiFi.begin(ssid, password);
  while (WiFi.status() != WL_CONNECTED) {
    delay(1000);
    Serial.println("Connecting...");
  }

  Serial.println(WiFi.localIP());
}


String processor(const String& var){
  //getSensorReadings();
  //Serial.println(var);
  if(var == "scan1"){
    return String(scan1);
  }
  else if(var == "scan2"){
    return String(scan2);
  }
  else if(var == "scan3"){
    return String(scan3);
  }
  return String();
}


const char index_html[] PROGMEM = R"rawliteral(
</html><!DOCTYPE HTML><html>
<head>
  <title>ESP Web Server</title>
  <meta name="viewport" content="width=device-width, initial-scale=1">
  <link rel="stylesheet" href="https://use.fontawesome.com/releases/v5.7.2/css/all.css" integrity="sha384-fnmOCqbTlWIlj8LyTjo7mOUStjsKC4pOpQbqyi7RrhN7udi9RwhKkMHpvLbHG9Sr" crossorigin="anonymous">
  <link rel="icon" href="data:,">
  <style>
    html {font-family: Arial; display: inline-block; text-align: center;}
    p { font-size: 1.2rem;}
    body {  margin: 0;}
    .topnav { overflow: hidden; background-image: linear-gradient(to bottom right, rgba(50, 192, 243, 0.5),rgba(27, 55, 131, 0.5), rgba(2, 251, 255, 0.6)); color: white; font-size: 1rem; }
    .content { padding: 20px; }
    .card { background-color: white; box-shadow: 2px 2px 12px 1px rgba(140,140,140,.5); }
    .cards { max-width: 800px; margin: 0 auto; display: grid; grid-gap: 2rem; grid-template-columns: repeat(auto-fit, minmax(400px, 1fr)); }
    .reading { font-size: 1.4rem; }
  </style>
</head>
<body>
  <div class="topnav">
    <h1>ForkLift Project</h1>
    <h1>QR Code & Data Read</h1>
  </div>
  <div class="content">
    <div class="cards">
      <div class="card">
        <p>Storage Cabinet</p><p><span class="reading"><span id="storageCabinet">###</span></p>
      </div>
      <div class="card">
        <p>Floor</p><p><span class="reading"><span id="floor">###</span></p>
      </div>
      <div class="card">
        <p>Type</p><p><span class="reading"><span id="type">###</span></p>
      </div>
    </div>
  </div>
  <br>
  <br>
  <br>
<script>
if (!!window.EventSource) {
 var source = new EventSource('/events');
 
 source.addEventListener('open', function(e) {
  console.log("Events Connected");
 }, false);
 source.addEventListener('error', function(e) {
  if (e.target.readyState != EventSource.OPEN) {
    console.log("Events Disconnected");
  }
 }, false);
 
 source.addEventListener('message', function(e) {
  console.log("message", e.data);
 }, false);
 
 source.addEventListener('storageCabinet', function(e) {
  console.log("storageCabinet", e.data);
  document.getElementById("storageCabinet").innerHTML = e.data;
 }, false);
 
 source.addEventListener('floor', function(e) {
  console.log("floor", e.data);
  document.getElementById("floor").innerHTML = e.data;
 }, false);
 
 source.addEventListener('type', function(e) {
  console.log("type", e.data);
  document.getElementById("type").innerHTML = e.data;
 }, false);
}
</script>
</body>
</html>)rawliteral";


void onQrCodeTask(void *pvParameters)
{
  struct QRCodeData qrCodeData;

  while (true)
  { if (newQR){
      if (reader.receiveQrCode(&qrCodeData, 100))
      {
        Serial.println("Found QRCode");
        if (qrCodeData.valid)
        {
          newQR = false;
          String qrCodePayload = (const char *)qrCodeData.payload;
          Serial.print("Payload: ");
          Serial.println(qrCodePayload);  

          if (qrCodePayload != scan1)
          {
            const char* t_type = "miss";

            int storageCabinetAndFloor[2];
            char type[64];
            //char BUFFER[64];
            decodeData(storageCabinetAndFloor, type, (char *)qrCodeData.payload);
            int storageCabinet = storageCabinetAndFloor[0];
            int floor = storageCabinetAndFloor[1];


            //MAKE OWN DECODE/ENCODE METHOD
            //bool asDecode = decodeJson(scan);
            //if (asDecode) {
            //  t_type = getType();
            //}

            Serial.print(type);
            Serial.print(storageCabinet);
            Serial.print(floor);

            // Send Events to the Web Server with the Sensor Readings
            events.send("ping",NULL,millis());
            events.send(String(type).c_str(),"type",millis());
            events.send(String(storageCabinet).c_str(),"storageCabinet",millis());
            events.send(String(floor).c_str(),"floor",millis());


          }
                
        }
        else
        {
          Serial.print("Invalid: ");
          Serial.println((const char *)qrCodeData.payload);
        }
      }
      vTaskDelay(100 / portTICK_PERIOD_MS);
    }
    else{
      while (Serial.available() == 0) {
      }
      int input = Serial.parseInt();
      if(input==1){
        newQR = true;
      }
    }
  }
}

void setup()
{
  newQR = true;
  Serial.begin(115200);
  Serial.println();

  //your other setup stuff...
  
  // Init WiFi
  initWiFi2();
  // Handle Web Server
  server.on("/", HTTP_GET, [](AsyncWebServerRequest *request){
    request->send_P(200, "text/html", index_html, processor);
  });

  // Handle Web Server Events
  events.onConnect([](AsyncEventSourceClient *client){
    if(client->lastId()){
      Serial.printf("Client reconnected! Last message ID that it got is: %u\n", client->lastId());
    }
    // send event with message "hello!", id current millis
    // and set reconnect delay to 1 second
    client->send("hello!", NULL, millis(), 10000);
  });
  server.addHandler(&events);
  server.begin();


  reader.setup();

  Serial.println("Setup QRCode Reader");

  reader.beginOnCore(1);

  Serial.println("Begin on Core 1");

  xTaskCreate(onQrCodeTask, "onQrCode", 4 * 1024, NULL, 4, NULL);
}

void loop()
{
  delay(100);
}

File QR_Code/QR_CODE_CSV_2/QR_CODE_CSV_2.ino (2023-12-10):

#include <ezButton.h>
#include <AccelStepper.h>
#include <MultiStepper.h>

#include <ESP32CameraPins.h>
#include <ESP32QRCodeReader.h>

#include <WiFi.h>
#include <HTTPClient.h>
#include <ESPAsyncWebServer.h>
#include <esp_camera.h>
#include "qrcode.h"

#include <ArduinoJson.h>
#include <strings.h>
#include "soc/soc.h"
#include "soc/rtc_cntl_reg.h"


// -------------------------------------------------------//
// ------------- WIFI / SERVER CONFIG ------------------- //
// -------------------------------------------------------//

// Wi-Fi credentials
const char* ssid = "Lolo";
const char* password = "jesuispauvre";

// Server configuration
const int serverPort = 80;

// Create an instance of the web server
AsyncWebServer server(serverPort);

// Server configuration
const char* serverAddress = "http://192.168.42.122:3000/processQrCode"; // Replace with your computer's IP address


// -------------------------------------------------------//
// ---------------- CAMERA CONFIG ----------------------- //
// -------------------------------------------------------//

// Camera configuration
ESP32QRCodeReader reader(CAMERA_MODEL_AI_THINKER);


// -------------------------------------------------------//
// ------------------ LED CONFIG ------------------------ //
// -------------------------------------------------------//

#define LED_BUILTIN 4

// Initialize LED
void initFlash() { 
  pinMode(LED_BUILTIN, OUTPUT);
}

// Turn on LED
void turnOnFlash() {
  digitalWrite(LED_BUILTIN, HIGH);  // Set LEDC duty cycle to maximum (255)
}

// Turn off LED
void turnOffFlash() {
  digitalWrite(LED_BUILTIN, LOW);  // Set LEDC duty cycle to 0 (off)
}


// -------------------------------------------------------//
// ----------- SERVER SCAN REQUEST CONFIG --------------- //
// -------------------------------------------------------//

// Flag to indicate if a scan is in progress
bool scanning = false;
bool newQR = true;
bool send_success = false;

// Route handler for the POST request to start a scan
void handleStartScan(AsyncWebServerRequest* request) {
  if (request->method() == HTTP_POST) {
    // Check if a scan is already in progress
    if (scanning) {
      request->send(200, "text/plain", "Scan already in progress");
      Serial.println("Scan already in progress");
    } 

    else {
      // Start the scan
      request->send(200, "text/plain", "Scan started");
      Serial.println("Scan started");
      scanning = true;
      newQR = true;
    }
  }
}


// -------------------------------------------------------//
// ----------- SCAN QR CODE CONFIG / HANDLE ------------- //
// -------------------------------------------------------//

String scan = "No Scan";

// Task on what to do when a QR code is found
void onQrCodeTask(void *pvParameters)
{
  
  Serial.print("onQRCodeData is called");
  struct QRCodeData qrCodeData;
  Serial.print("there is a new qr :");
  Serial.print(newQR==1);
  
  while (true)
  { 
    delay(200);
    Serial.print(".");
    if(scanning){
      //qrCodeData = {false, 0, {0}, 0};
      //memset(payload, 0, sizeof(payload));
      if (newQR)
      {
        if (reader.receiveQrCode(&qrCodeData, 100))
        {
          // ESP32 find QR Code
          Serial.println("Found QRCode");

          // Check if QR code is valid 
          if (qrCodeData.valid)
          {


            // String that is on the qr code
            String qrCodePayload = (const char *)qrCodeData.payload;

            Serial.print("scan : ");
            Serial.println(qrCodePayload);  

            // Check if this is a new qr code
            if (qrCodePayload != scan)
            {
              newQR = false;
              Serial.println("this was a new QR Code");

              // Send the ID to the server until success 
              while(!send_success){
                sendIdToServer(qrCodePayload.c_str());
                Serial.println("Sending ID to server...");

                if (send_success){
                  Serial.println("ID sent to server");

                  //do a flash to confirm that id was sent to server
                  turnOnFlash();
                  delay(400);
                  turnOffFlash();
                  delay(400);
                  turnOnFlash();
                  delay(100);
                  turnOffFlash();

                  newQR = true;
                  scanning = false;
                }
                else{
                  Serial.println("Error sending ID to server");
                  Serial.println("Retrying...");
                }
              }
              scan = qrCodePayload;
              send_success = false;
              //qrCodeData = {false, 0, {0}, 0};
            }
          }
          else
          {
            Serial.print("Invalid: ");
            Serial.println((const char *)qrCodeData.payload);
          }
        }
        vTaskDelay(100 / portTICK_PERIOD_MS);
      }
      else
      {
        while (Serial.available() == 0) {
        }
        int input = Serial.parseInt();
        if (input == 1){
          newQR = true;
        }
      }

    }
  }
}


// -------------------------------------------------------//
// ------------- WIFI CONNECTION CONFIG ----------------- //
// -------------------------------------------------------//

// Connect to Wi-Fi network
void connectToWiFi() {
  WiFi.begin(ssid, password);
  Serial.print("Connecting to Wi-Fi");
  while (WiFi.status() != WL_CONNECTED) {
    delay(500);
    Serial.print(".");
  }
  Serial.println("\nConnected to Wi-Fi");
}


// -------------------------------------------------------//
// --------- HANDLE SENDING ID TO SERVER ---------------- //
// -------------------------------------------------------//

// Send ID number to the server via HTTP
void sendIdToServer(const char* id) {
  HTTPClient http;
  String requestUrl = serverAddress;
  requestUrl += "?id=";
  requestUrl += id;

  Serial.print("Request URL: ");
  Serial.println(requestUrl);

  http.begin(requestUrl);
  int httpResponseCode = http.GET();
  
  if (httpResponseCode > 0) {
    String response = http.getString();
    Serial.println("Server response: " + response);
    send_success = true;
    // Process the response and take appropriate action
  } else {
    Serial.println("Error sending request to the server");
    send_success = false;
  }
  Serial.print("end of sendIdToServer");
  
  http.end();
}


// -------------------------------------------------------//
// --------------- MAIN CONFIGURATION ------------------- //
// -------------------------------------------------------//
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

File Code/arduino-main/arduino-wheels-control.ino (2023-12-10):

void setDirection(Instruction direction) 
{
  switch(direction) {
    case Forward:
      forward();
      break;
    case Backward:
      backward();
      break;
    case Left:
      left();
      break;
    case Right:
      right();
      break;
    case TurnLeft:
      turnCounterClockwise();
      break;
    case TurnRight:
      turnClockwise();
      break;
    case Stop:
      stop();
      break;
    default:
      break;
  }

}

void move()
{
  for (int i = 0; i < 4; i++)
  {
    wheels[i].runSpeed();
  }
}

void forward()
{
  wheels[FRONT_RIGHT_IDX].setSpeed(-speed);
  wheels[FRONT_LEFT_IDX].setSpeed(-speed);
  wheels[BACK_RIGHT_IDX].setSpeed(-speed);
  wheels[BACK_LEFT_IDX].setSpeed(-speed);
}

void backward()
{
  wheels[FRONT_RIGHT_IDX].setSpeed(speed);
  wheels[FRONT_LEFT_IDX].setSpeed(speed);
  wheels[BACK_RIGHT_IDX].setSpeed(speed);
  wheels[BACK_LEFT_IDX].setSpeed(speed);
}

void left()
{
  wheels[FRONT_RIGHT_IDX].setSpeed(-speed);
  wheels[FRONT_LEFT_IDX].setSpeed(speed);
  wheels[BACK_RIGHT_IDX].setSpeed(speed);
  wheels[BACK_LEFT_IDX].setSpeed(-speed);
}

void right()
{
  wheels[FRONT_RIGHT_IDX].setSpeed(speed);
  wheels[FRONT_LEFT_IDX].setSpeed(-speed);
  wheels[BACK_RIGHT_IDX].setSpeed(-speed);
  wheels[BACK_LEFT_IDX].setSpeed(speed);
}

void turnClockwise()
{
  wheels[FRONT_RIGHT_IDX].setSpeed(speed);
  wheels[FRONT_LEFT_IDX].setSpeed(-speed);
  wheels[BACK_RIGHT_IDX].setSpeed(speed);
  wheels[BACK_LEFT_IDX].setSpeed(-speed);
}

void turnCounterClockwise()
{
  wheels[FRONT_RIGHT_IDX].setSpeed(-speed);
  wheels[FRONT_LEFT_IDX].setSpeed(speed);
  wheels[BACK_RIGHT_IDX].setSpeed(-speed);
  wheels[BACK_LEFT_IDX].setSpeed(speed);
}

void diagonalFrontLeft()
{
  wheels[FRONT_RIGHT_IDX].setSpeed(speed);
  wheels[FRONT_LEFT_IDX].setSpeed(-speed);
  wheels[BACK_RIGHT_IDX].setSpeed(-speed);
  wheels[BACK_LEFT_IDX].setSpeed(speed);
}

void stop()
{
  brake();
  delay(500);
  enabled = false;
  digitalWrite(enablePin, HIGH); // Disconnect motors
}

void brake() 
{
  wheels[FRONT_RIGHT_IDX].setSpeed(0);
  wheels[FRONT_LEFT_IDX].setSpeed(0);
  wheels[BACK_RIGHT_IDX].setSpeed(0);
  wheels[BACK_LEFT_IDX].setSpeed(0);
}

void enable()
{
  enabled = true;
  digitalWrite(enablePin, LOW); // Connect motors
}
